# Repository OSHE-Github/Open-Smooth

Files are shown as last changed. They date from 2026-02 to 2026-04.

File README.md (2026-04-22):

# Open-Smooth

# Project Overview
OPENSmooth introduces an open-source 3D print post-processor that uses acetone vapor and heat to smooth filament layer lines. The system integrates electronic monitors to regulate exposure time and ensure safe operation, reducing risks associated with manual methods. By combining automated vapor control with real-time safety monitoring, the design provides a low-cost, accessible solution to improve the surface quality of 3D-printed parts.
# Bill of Materials

### Physical Construction
| Category | Item | Part Number | Source | Cost |
|---|---|---|---|---|
| Physical Construction | PETG filament | - | Amazon | $15 (per spool) |
| Physical Construction | Enclosure bin | - | Amazon | $12 |
| Physical Construction | Plastic bottles | - | Amazon | $7 |
| Physical Construction | Fan grill | - | Amazon | $5 |
| Physical Construction | Epoxy | - | Amazon | $8 |

### Electronics
| Category | Item | Part Number | Source | Cost |
|---|---|---|---|---|
| Electronics | Heater | - | Amazon | $35 |
| Electronics | Atomizers | - | Amazon | $23 |
| Electronics | Fans (x2) | - | Amazon | $18 |
| Electronics | E-stop | - | Amazon | $12 |
| Electronics | Touchscreen | - | Amazon | $16 |
| Electronics | Servo | - | Amazon | $19 |
| Electronics | IEC plug | - | Amazon | $8 |
| Electronics | IEC cable | - | Amazon | $6 |
| Electronics | RGB lights | - | Amazon | $13 |

### Circuitry
| Category | Item | Part Number | Source | Cost |
|---|---|---|---|---|
| Circuitry | PCB | - | - | $10 |
| Circuitry | Arduino Mega | - | - | $30 |
| Circuitry | ATMEGA328 (x2) | - | DigiKey | $6 |
| Circuitry | Relays (x2) | - | Amazon | $14 |
| Circuitry | Buck converters | - | Amazon | $8 |
| Circuitry | 2N2222A Transistors (x20) | - | DigiKey | $1 |
| Circuitry | Thermistor | - | - | $8 |
| Circuitry | Acetone sensor | - | - | $8 |
| Circuitry | 12V power supply | - | Amazon | $10 |

### Consumables
| Category | Item | Part Number | Source | Cost |
|---|---|---|---|---|
| Consumables | Acetone | - | Amazon | $10 |
| Consumables | Carbon pellets | - | Amazon | $12 |

---

## Tools Used

### Testing and Planning
| Category | Item | Part Number | Source | Cost |
|---|---|---|---|---|
| Testing and Planning | Breadboard | ZYJ-102 | Adafruit | $5.95 |
| Testing and Planning | Multimeter | Fluke 179 | Fluke | $479.99 |
| Testing and Planning | Oscilloscope | MSO6012A | Test Equity | $2955.00 |

### Assembly
| Category | Item | Part Number | Source | Cost |
|---|---|---|---|---|
| Assembly | Solder Iron | FX-888D | Hakko | $121.47 |
| Assembly | Dremel | - | Milwaukee | - |
| Assembly | Drill | - | Milwaukee | - |

### Programming
| Category | Item | Part Number | Source | Cost |
|---|---|---|---|---|
| Programming | Arduino IDE | Arduino IDE 2.3.2 | Arduino | $0 |

# Assembly Overview
### 1. Print All Components
- 3D print all required parts using PETG filament
- Base components (13 parts)
- Filter components (9 parts)
- Rotating table components (4 parts) + servo housing (1 part)
- Recommended to have ~2kg of filament available
- Use supports only where necessary (mainly the table)

### 2. Assemble the Base
- Fit all base components together using the dovetail joints
- Ensure correct orientation (parts only fit one way)
- Press-fit assembly should hold the structure together
- Apply epoxy if additional strength is needed

### 3. Prepare and Assemble the Lid
- Cut and drill openings for:
  - Heater (rear-center)
  - Filter (top-center)
- Mount heater:
  - Cut a circular hole for the heater body
  - Drill mounting holes
  - Install the gasket and secure the heater
- Mount filter:
  - Cut a square intake hole
  - Drill mounting holes (M3)
- Install a limit switch at the bottom edge of the lid to detect the open/closed state

### 4. Assemble and Install the Filter
- Assemble the main filter housing using M3 screws
- Install a 60 mm fan and secure it with M4 screws
- Prepare pellet drawer:
  - Epoxy if printed in two parts
  - Fill with carbon pellets
- Insert pellet drawer and secure with clips and screws
- Cut mounting holes and vent in enclosure
- Attach filter and gasket to enclosure

### 5. Install the Rotating Table System
- Mount the servo into the servo housing
- Route wires through housing cutouts
- Install housing into base (center cutout)
- Attach the spur gear to the servo shaft
- Install the table spacer and the rotating table
- Snap the fan grille into place

### 6. Assemble Atomizers
- Assemble each atomizer:
  - Insert wick into atomizer
  - Secure wick using trimmed nail or pin
- Extend wiring to reach the control PCB
- Repeat for all atomizers
- Fill with acetone and place into holders

### 7. Final Assembly & Integration
- Ensure all mechanical components are secured
- Verify moving parts (table rotation, fan clearance)
- Confirm proper placement of heater, filter, and sensors
- Connect electronics (fans, heater, atomizers, sensors, etc.)
- Perform a system check before operation

### 8. Final Checks
- Verify all fasteners are tight
- Ensure no air leaks around the filter and heater
- Confirm limit switch functionality
- Test electrical connections safely

**Note:**  
Epoxy is optional in most areas but recommended for long-term durability.

# Future Improvements
### Enclosure Stability and Sealing Capability
The enclosure currently uses duct tape to keep a seal with the lid. This works well, but it could be improved. Adding a lid locking mechanism with a layered rubber seal at the base would prevent the lid from unintentionally opening as well as provide a better seal.

### Atomizer bottles
The atomizer bottles we used for this project are made of PET plastic. PET plastic is susceptible to acetone over long periods of time, causing the bottles to likely leak. In our testing, the bottles showed minimal wear, but this doesn't mean they are 100% safe. Bottles made of PP or HDPE plastic would be much better suited for this application.

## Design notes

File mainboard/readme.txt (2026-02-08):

Here is the code and kicad progect for the mainboard and pcb

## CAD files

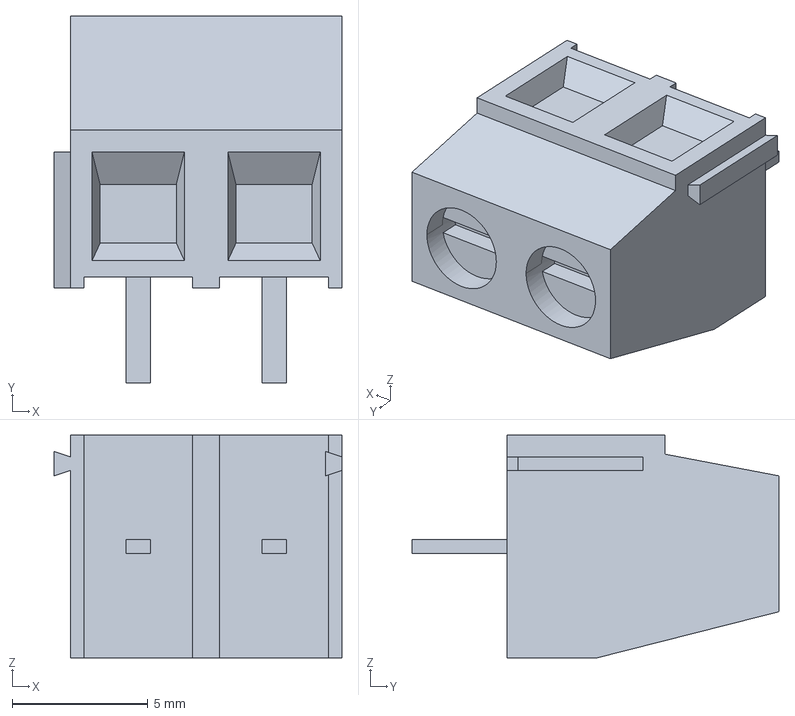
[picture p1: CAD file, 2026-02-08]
mainboard/pcb/KiCADv6/c-282836-2-j-3d.stp
10.6 x 13.5 x 8.20 mm

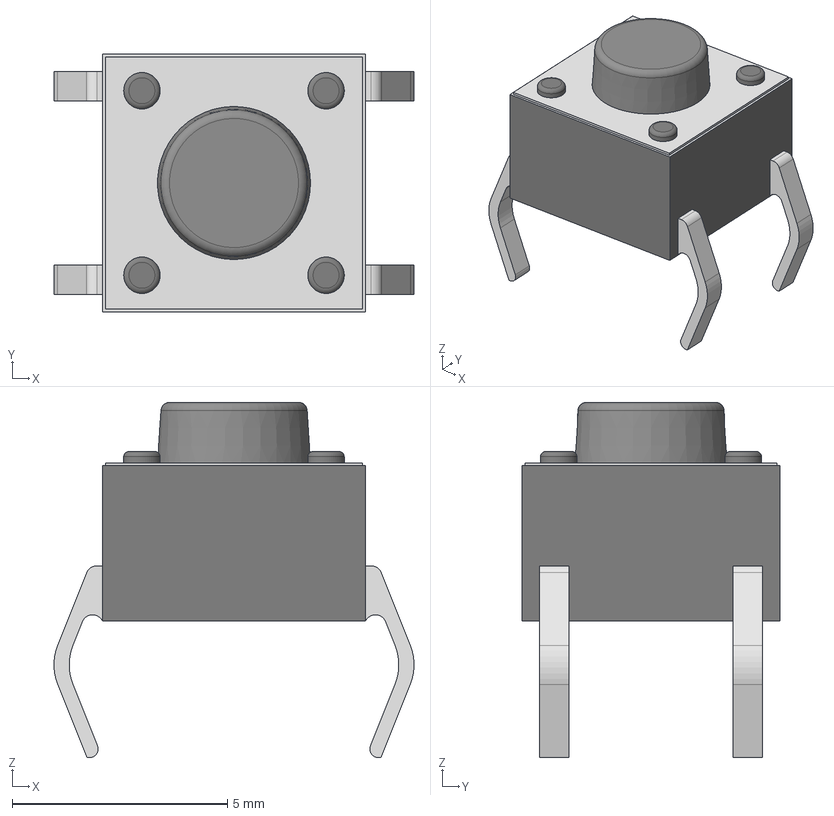
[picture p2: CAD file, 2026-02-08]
mainboard/pcb/Tactal Switch -THru (6mmx 6mmx5mm)-Black.stp
8.37 x 5.99 x 8.26 mm

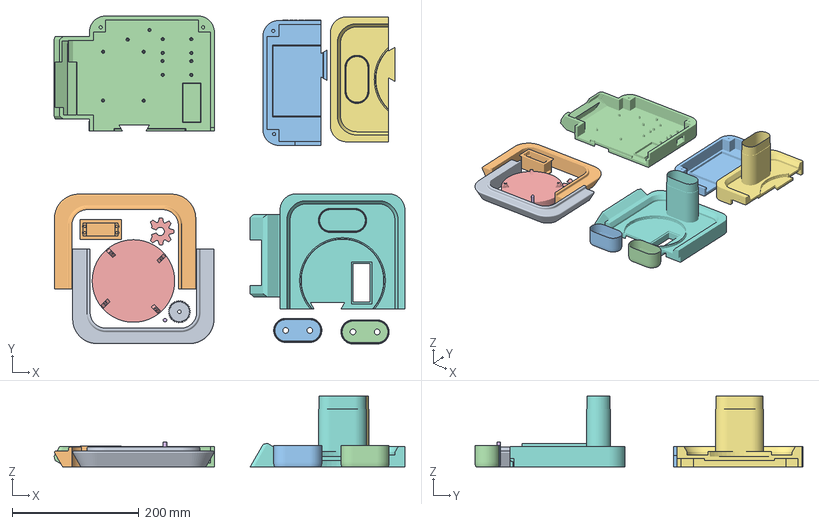
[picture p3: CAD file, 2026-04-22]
OPENSmooth_EnclosureS26 (1).3mf
552.9 x 516.8 x 111.6 mm
Final Assembly_48
Final Assembly_51
Final Assembly_53
Final Assembly_82
Final Assembly_93
Final Assembly_96
Final Assembly_67_A
Final Assembly_67_B
Final Assembly_92_A
Final Assembly_92_B
Final Assembly_16_A
Final Assembly_16_B
Revolving Table (1)

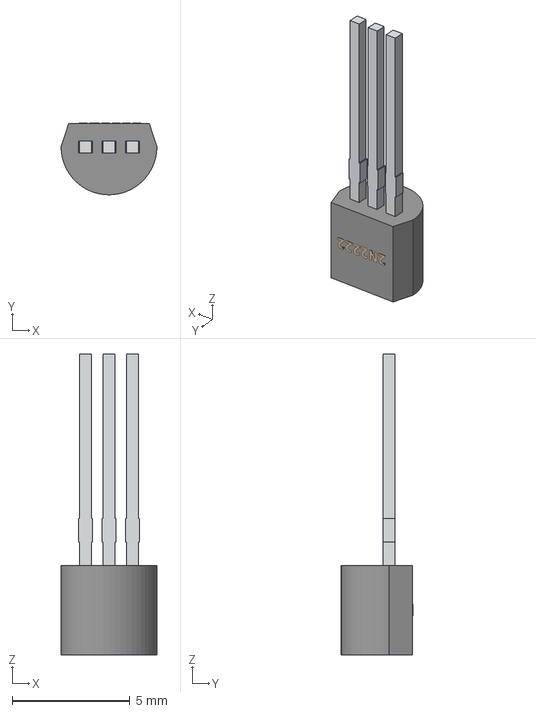
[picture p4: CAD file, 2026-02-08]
mainboard/pcb/2n2222.step
4.08 x 3.05 x 12.8 mm

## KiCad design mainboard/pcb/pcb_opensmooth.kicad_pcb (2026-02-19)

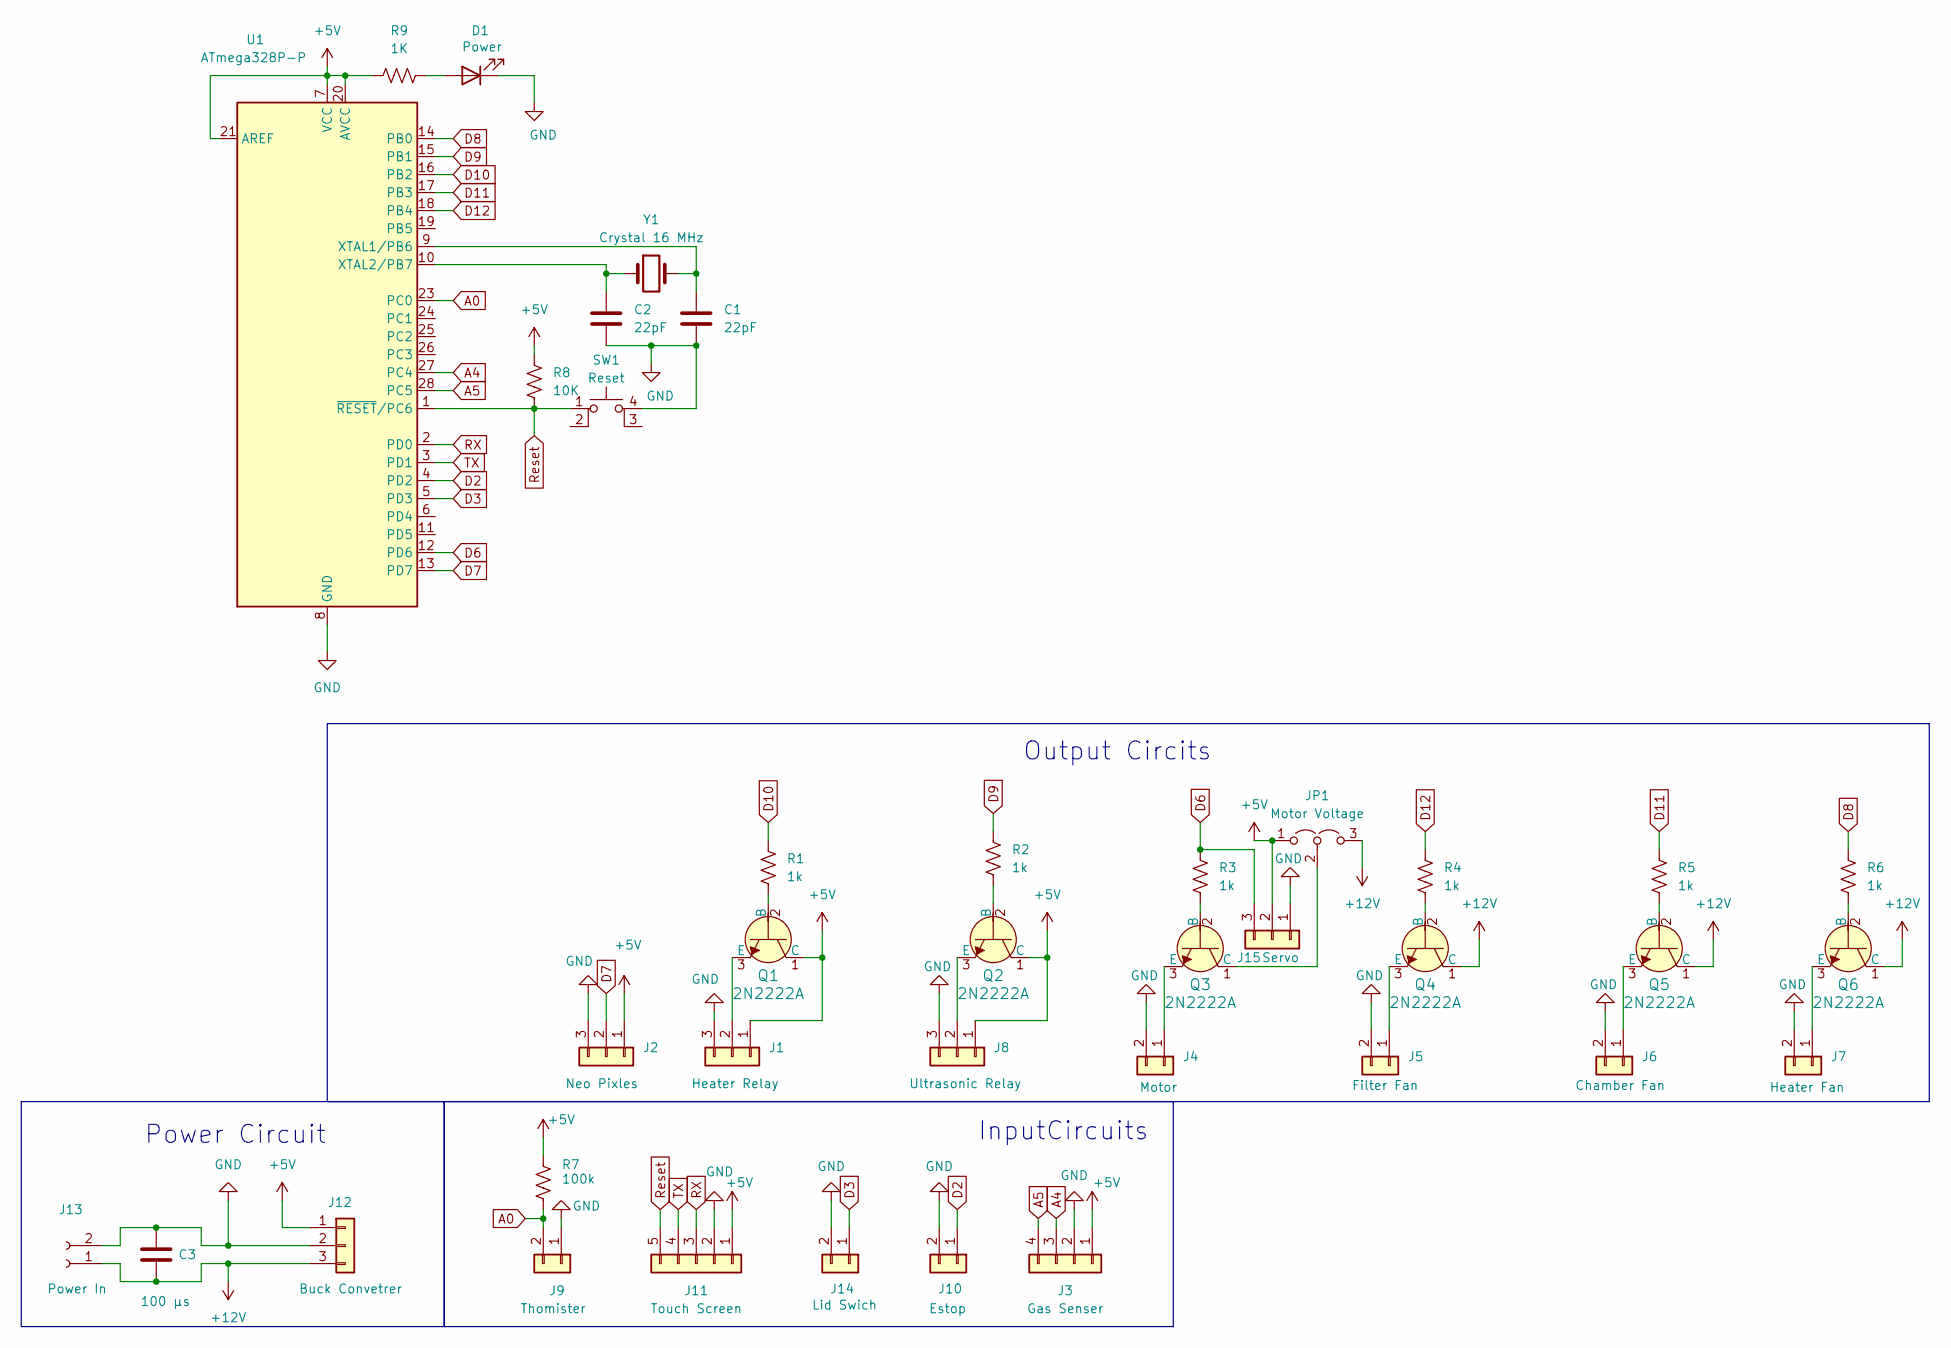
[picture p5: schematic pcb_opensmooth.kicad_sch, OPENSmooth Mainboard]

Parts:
C1, C2: 22pF; C_Disc_D3.0mm_W1.6mm_P2.50mm
C3: 100 μs; C_Radial_D6.3mm_H7.0mm_P2.50mm
D1: Power; LED_D5.0mm
J1: Heater Relay; JST_XH_B3B-XH-A_1x03_P2.50mm_Vertical
J2: Neo Pixles; JST_XH_B3B-XH-A_1x03_P2.50mm_Vertical
J3: Gas Senser; JST_XH_B4B-XH-A_1x04_P2.50mm_Vertical
J4: Motor; JST_XH_B2B-XH-A_1x02_P2.50mm_Vertical
J5: Filter Fan; JST_XH_B2B-XH-A_1x02_P2.50mm_Vertical
J6: Chamber Fan; JST_XH_B2B-XH-A_1x02_P2.50mm_Vertical
J7: Heater Fan; JST_XH_B2B-XH-A_1x02_P2.50mm_Vertical
J8: Ultrasonic Relay; JST_XH_B3B-XH-A_1x03_P2.50mm_Vertical
J9: Thomister; JST_XH_B2B-XH-A_1x02_P2.50mm_Vertical
J10: Estop; JST_XH_B2B-XH-A_1x02_P2.50mm_Vertical
J11: Touch Screen; JST_XH_B5B-XH-A_1x05_P2.50mm_Vertical
J12: Buck Convetrer; JST_XH_B3B-XH-A_1x03_P2.50mm_Vertical
J13: Power In; 282837-2_TYC
J14: Lid Swich; JST_XH_B2B-XH-A_1x02_P2.50mm_Vertical
J15: Servo; PinHeader_1x03_P2.54mm_Vertical
JP1: Motor Voltage; PinHeader_1x03_P2.54mm_Vertical
Q1, Q2, Q3, Q4, Q5, Q6: 2N2222A; 2n2222; MPN 2N2222A; Digi-Key_PN 2N2222ACS-ND
R1, R2, R3, R4, R5, R6: 1k; R_Axial_DIN0309_L9.0mm_D3.2mm_P12.70mm_Horizontal
R7: 100k; R_Axial_DIN0309_L9.0mm_D3.2mm_P12.70mm_Horizontal
R8: 10K; R_Axial_DIN0309_L9.0mm_D3.2mm_P12.70mm_Horizontal
R9: 1K; R_Axial_DIN0309_L9.0mm_D3.2mm_P12.70mm_Horizontal
SW1: Reset; Switch_Tactile_THT_6x6mm
U1: ATmega328P-P; DIP-28_W7.62mm
Y1: Crystal 16 MHz; Crystal_HC49-4H_Vertical

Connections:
+5V: J1.1, J2.1, J3.1, J8.1, J11.1, J12.1, J15.2, JP1.1 (A), Q1.1 (C), Q2.1 (C), R7.2, R8.2, R9.2, U1.7 (VCC), U1.20 (AVCC), U1.21 (AREF)
+12V: C3.2, J12.3, J13.1, JP1.3 (B), Q4.1 (C), Q5.1 (C), Q6.1 (C)
A0: J9.2, R7.1, U1.23 (PC0)
A4: J3.3, U1.27 (PC4)
A5: J3.4, U1.28 (PC5)
D2: J10.1, U1.4 (PD2)
D3: J14.1, U1.5 (PD3)
D6: J15.3, R3.2, U1.12 (PD6)
D7: J2.2, U1.13 (PD7)
D8: R6.2, U1.14 (PB0)
D9: R2.2, U1.15 (PB1)
D10: R1.2, U1.16 (PB2)
D11: R5.2, U1.17 (PB3)
D12: R4.2, U1.18 (PB4)
GND: C1.2, C2.2, C3.1, D1.1 (K), J1.3, J2.3, J3.2, J4.2, J5.2, J6.2, J7.2, J8.3, J9.1, J10.2, J11.2, J12.2, J13.2, J14.2, J15.1, SW1.4 (A), U1.8 (GND), U1.22 (GND)
unnamed: D1.2 (A), R9.1
unnamed: J1.2, Q1.3 (E)
unnamed: J4.1, Q3.3 (E)
unnamed: J5.1, Q4.3 (E)
unnamed: J6.1, Q5.3 (E)
unnamed: J7.1, Q6.3 (E)
unnamed: J8.2, Q2.3 (E)
unnamed: JP1.2 (C), Q3.1 (C)
unnamed: Q1.2 (B), R1.1
unnamed: Q2.2 (B), R2.1
unnamed: Q3.2 (B), R3.1
unnamed: Q4.2 (B), R4.1
unnamed: Q5.2 (B), R5.1
unnamed: Q6.2 (B), R6.1
unnamed: C1.1, U1.9 (XTAL1/PB6), Y1.2
unnamed: C2.1, U1.10 (XTAL2/PB7), Y1.1
RX: J11.3, U1.2 (PD0)
Reset: J11.5, R8.1, SW1.1, U1.1 (~RESET/PC6)
TX: J11.4, U1.3 (PD1)

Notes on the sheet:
InputCircuits
Output Circits
Power Circuit

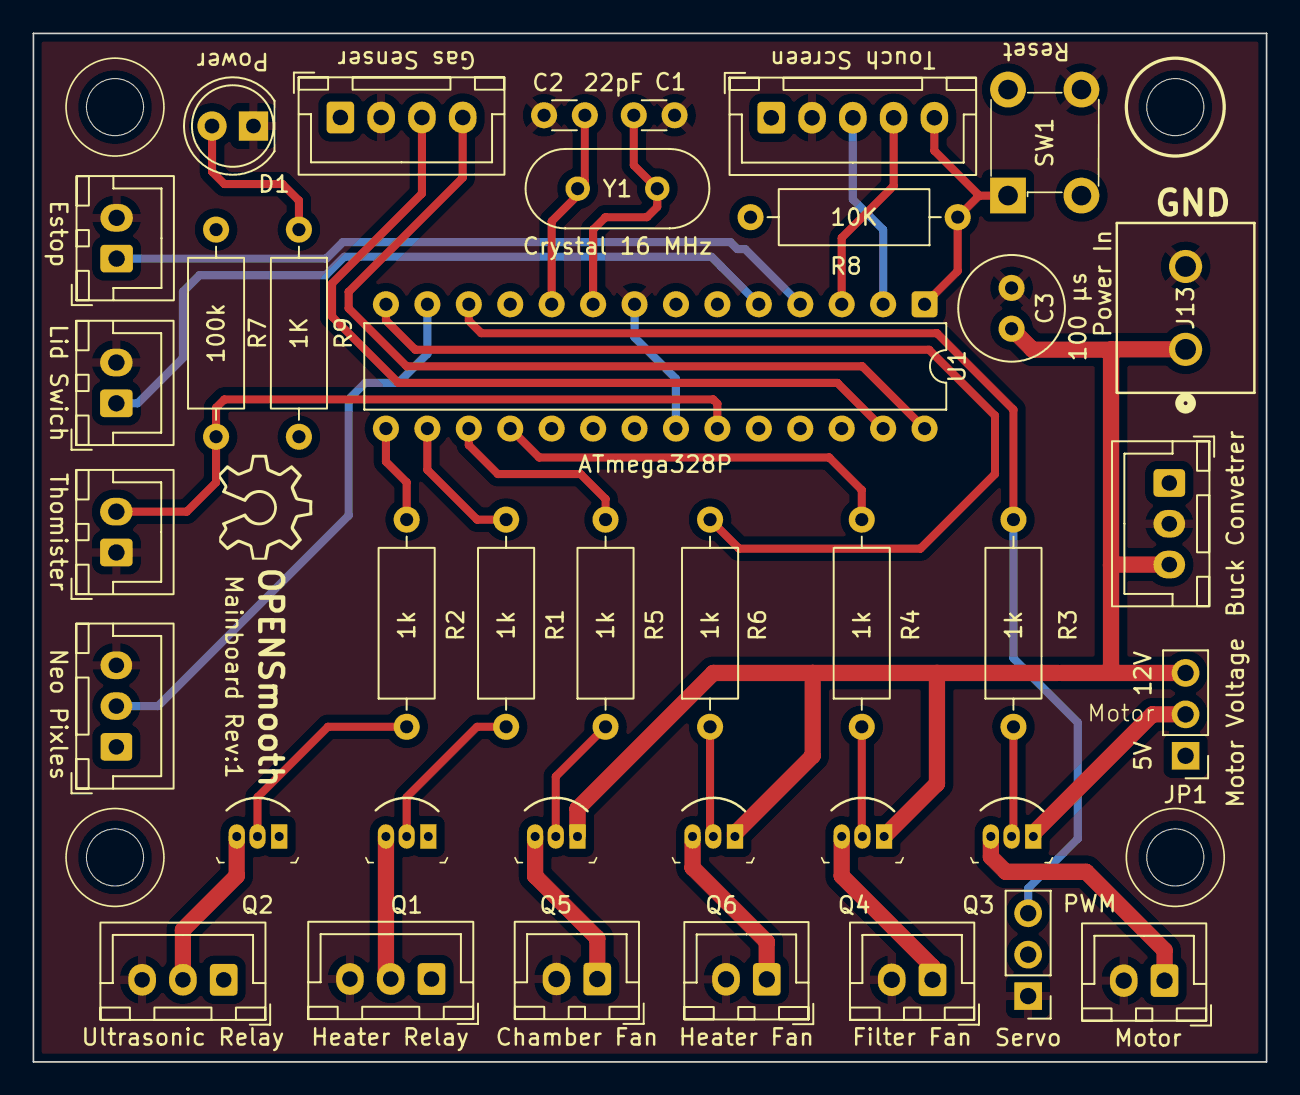
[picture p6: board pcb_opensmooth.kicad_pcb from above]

Board: 2 copper layers, 75.6 x 63.0 mm, 38 parts (0 on the bottom side), 34 nets.

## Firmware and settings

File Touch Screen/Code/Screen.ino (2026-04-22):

//incled parting file
#include "Parse.h"

//define touch screen and tft
TouchScreen ts = TouchScreen(XP, YP, XM, YM, 300);
Elegoo_TFTLCD tft(LCD_CS, LCD_CD, LCD_WR, LCD_RD, LCD_RESET);

int MButton = 67; 
int touchX = 180;
int touchY = 120;
int touchXOld = 180;
int touchYOld = 120;
uint16_t color[5][5];

//Setup code
void setup() {
  //start serial at 115200 baud rate
  Serial.begin(115200);
  Serial1.begin(115200);
  delay(1000);
  //mouse setup;
  pinMode(MButton, INPUT_PULLUP);
  pinMode(A11, INPUT);
  pinMode(A12, INPUT);



  //start tft and set roation
  tft.begin(0x9341);
  tft.setRotation(1);

  //pin setup for touchscreen and buzzer
  pinMode(13, OUTPUT);
  pinMode(SD_CS, OUTPUT);
  pinMode(buzzer+4, OUTPUT);
  digitalWrite(buzzer+4, LOW);
  pinMode(buzzer, OUTPUT);
  digitalWrite(LCD_CS, HIGH);
  pinMode(SD_CS, OUTPUT);
  digitalWrite(SD_CS, HIGH);

  delay(200);
  //inshalise SD card and report if failed
  if (!SD.begin(SD_CS)) {
    //Serial.println(F("SD failed!"));
    parse("Text(SD ERROR,50,100,4,65535)", tft);
    while (1)
      ;
  }


  //remove old files
  SD.remove(update);
  SD.remove(bFile);

  //run the starting file
  sd("begin.txt", tft);
  //mouse
  //mouse
  readColor();
}


//the runing body of the code
void loop() {

  //save screen touch to p
  digitalWrite(13, HIGH);
  TSPoint p = ts.getPoint();
  digitalWrite(13, LOW);
  pinMode(LCD_CS, OUTPUT);
  pinMode(LCD_CD, OUTPUT);

  mouse();
  //p.z = click();
  //check to see if screen was touched
  if (p.z > 15 || click()) {
    int temp = p.x;
    //convert the touch to quredents on screen
    p.x = map(p.y, 930, 40, 0, 320);
    p.y = map(temp, 900, 160, 0, 240);

    //mouse
    if(click()){
      p.x = touchX;
      p.y = touchY;
    }
    


    //extra delay to prevent double press
    delay(100);

    //check to see if a button was pressesd
    for (int i = 0; i < bCount; i++) {
      if (p.x > buttons[i][0] && p.x < buttons[i][2] && p.y > buttons[i][1] && p.y < buttons[i][3]) {

        //beep the buzzer
        for (int i = 0; i < 100000 / (2 * pitch) && Buzz; i++) {
          digitalWrite(buzzer, HIGH);
          delayMicroseconds(pitch);
          digitalWrite(buzzer, LOW);
          delayMicroseconds(pitch);
        }

        //if button was pressed open file and print line
        file = SD.open(bFile);
        //serch through the file until corect line is found
        for (int j = 0; j <= i; j++) {
          for (int k = 0; k < 40; k++) {
            Fileline[k] = file.read();
            if (Fileline[k] == 10) {
              Fileline[k] = 0;
              break;
            }
          }
        }
        //close the file
        file.close();
        delay(5);
        //run the file line
        parse(Fileline, tft);
        if (fileName[0] != 0) {
          sd(fileName, tft);
          fileName[0] = 0;
        }
        if (old == 1) {
          sd(OldFile, tft);
          old = 0;
        }
        parse("Run(text.txt)", tft);
        Time = millis();
        //mouse
        readColor();

        break;
      }
      
    }
  }

  if (Serial1.available()) {
    serial(Serial1.readStringUntil('\n').c_str(), tft);
    if (old == 1) {
      sd(OldFile, tft);
      old = 0;
    }
  }

  if (Time + UPDATE_TIME < millis()) {
    parse("Run(text.txt)", tft);
    x += 10;
    Time = millis();
  }
}

//mouse
int click(){
  if(!digitalRead(MButton)) return 30;
  return 0;
}
void mouse(){
  int Ax = analogRead(A11);
  int Ay = analogRead(A12);
  bool change = false;

  if(Ay < 300 && touchX < 315){
    touchX +=5;
    change = true;
  }
  if(Ay > 700 && touchX > 0){
    touchX -=5;
    change = true;
  }
  if(Ax > 700 && touchY < 235){
    touchY +=5;
    change = true;
  }
  if(Ax < 300 && touchY > 0){
    touchY -=5;
    change = true;
  }

  if(change){
    for(int i = 0; i < 5; i++){
      for(int j = 0; j < 5; j++){
        tft.drawPixel(touchXOld+i, touchYOld+j, color[i][j]);
        color[i][j] = tft.readPixel(touchX+i, touchY+j);
      }
    }
    touchXOld = touchX;
    touchYOld = touchY;
    tft.fillRect(touchX, touchY, 5, 5, 65535);
    tft.fillRect(touchX+1, touchY+1, 3, 3, 0);
    delay(15);
  }

}

void readColor(){
  for(int i = 0; i < 5; i++){
      for(int j = 0; j < 5; j++){
        color[i][j] = tft.readPixel(touchX+i, touchY+j);
      }
    }
    touchXOld = touchX;
    touchYOld = touchY;
    tft.fillRect(touchX, touchY, 5, 5, 65535);
    tft.fillRect(touchX+1, touchY+1, 3, 3, 0);
}

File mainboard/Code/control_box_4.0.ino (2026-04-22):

#include <Adafruit_NeoPixel.h>
#include <Servo.h>

#include "Thermister.h"
#include "Vars.h"
#include "Heater.h"
#include "Acetone.h"



//libray setup
NTC_100k tempSence(thmist);
RelayHeater heater(heaterPin, fan1, tempSence);
bomb acetone(ultrasonic, fanHeater);
Servo servo;
Adafruit_NeoPixel neo(ledCount, 7, NEO_GRB + NEO_KHZ800 );

void setup() {
  //inishalise Serial
  Serial.begin(115200);
  neo.begin();
  

  while (!Serial) { delay(10); }  // Wait for serial console to open
  //set up gas sencer in acetone
  acetone.Setup();
  //chamber fan setup
  pinMode(fanPin, OUTPUT);
  pinMode(button, INPUT_PULLUP);
  pinMode(encloser, INPUT_PULLUP);
  //estop
  //attachInterrupt(digitalPinToInterrupt(button), stop, LOW);
  //servo setup
  servo.attach(6);

  //screen turn on
  digitalWrite(fanPin,LOW);
  delay(1000);
  digitalWrite(fanPin,HIGH);
  //color(neo.Color(255, 255, 255));

}

void loop() {
  update(timer > 0);


  if (time + 2000 < millis()) {
    if (timer > 0) timer--;
    send();
    time = millis();
  }

  read();
}

//update sencers
//need to rewrite
void update(bool ace) {

  if (!digitalRead(button)){
    delay(500);
    if (!digitalRead(button)) stop();
  }

  if (digitalRead(encloser) == 1 && open) {
    //pauses system if lid is opened
    heater.run();
    acetone.run(ace);
    Serial.println("CLOSE");
    open = false;
  } else if (digitalRead(encloser) == 1) {
    //updates heater and acetone
    heater.run();
    acetone.run(ace);
  } else {
    //pauses system if lid is opened
    heater.pause();
    acetone.pause();
    servo.write(90);
    if(!open) Serial.println("OPEN");
    open = true;
  }
  //estop if max temp is reached
  //if (heater.read(false) >= heatMax) stop();
}

//reads in serial and sends to parce
void read() {
  String in;
  String comand;
  int space;
  double input;
  if (Serial.available()) {

    in = Serial.readStringUntil('\n');  // Read until newline
    space = in.indexOf(" ");            // find space
    if (space != -1) {
      //if there is a space split in comand in 2
      comand = in.substring(0, space);
      input = in.substring(space + 1).toDouble();
    } else {
      //only send comand
      comand = in;
      input = 0;
    }
    //send comands to be parsed
    set(comand, input);
  }
}

//parse the comand and give its input
void set(String comand, double input) {
  //all of the parsing
  comand.trim();
  if (comand.equalsIgnoreCase("setTemp")) heater.setTemp(input, farenhight);
  else if (comand.equalsIgnoreCase("setAcetone")) acetone.setAcetone(input);
  else if (comand.equalsIgnoreCase("setFilter")) {
    if (input == 0) acetone.runFilter(false);
    else acetone.runFilter(true);
  } else if (comand.equalsIgnoreCase("setHeatFan")) {
    if (input == 0) heater.runFan(false);
    else heater.runFan(true);
  } else if (comand.equalsIgnoreCase("setCircFan")) {
    if (input == 0) fan = false;
    else fan = true;
  } else if (comand.equalsIgnoreCase("setServo")) {
    if (input == 0) servo.write(90);
    else servo.write(105);
  } else if (comand.equalsIgnoreCase("Run")) {
    timer = (int)input;
  } else if (comand.equalsIgnoreCase("KILL")) {
    stop();
  } else if (comand.equalsIgnoreCase("RED")) {
    color(neo.Color(255, 0, 0));
  } else if (comand.equalsIgnoreCase("GREEN")) {
    color(neo.Color(0, 255, 0));
  } else if (comand.equalsIgnoreCase("BLUE")) {
    color(neo.Color(0, 0, 255));
  } else if (comand.equalsIgnoreCase("YELLOW")) {
    color(neo.Color(255, 255, 0));
  } else if (comand.equalsIgnoreCase("WHITE")) {
    color(neo.Color(255, 255, 255));
  } else if (comand.equalsIgnoreCase("PURPLE")) {
    color(neo.Color(135, 0, 255));
  } else if (comand.equalsIgnoreCase("BLACK")) {
    color(neo.Color(0, 0, 0));
  } else Serial.println("Unknown Comand");
}

//sets the leds a color
void color(uint32_t color) {
  for (int i = 0; i < ledCount; i++)
    neo.setPixelColor(i, color);
  neo.show();
}

//sends info to screen
void send() {
  Serial.print("TEMP ");
  Serial.println((int)heater.read(farenhight));
  Serial.print("TempTarget ");
  Serial.println((int)heater.curentSet(farenhight));
  Serial.print("ACETONE ");
  Serial.println((acetone.getAcetone()));
  Serial.print("AcetoneTarget ");
  Serial.println(((int)acetone.getPresent()));
  // Serial.print(" Fans: ");
  // if (heater.curentFan()) Serial.print(1);
  // else Serial.print(0);
  // if (acetone.getFilter()) Serial.print(1);
  // else Serial.print(0);
  // if (fan) Serial.print(1);
  // else Serial.print(0);
  // Serial.print(" Timer: ");
  // Serial.println(timer);
}

//estop. stop all prosesed exsept fan
void stop() {
  detachInterrupt(digitalPinToInterrupt(button));
  heater.kill();
  acetone.kill();
  servo.write(90);
  digitalWrite(fanPin, HIGH);
  // Serial.println("KILL");
  while (true)
    Serial.println("KILL");
}

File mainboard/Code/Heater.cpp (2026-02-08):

// Author: Austin Deegan
// Date: 10/20/25
// Discription: controls a heater with bang bang controls

#include "Heater.h"
#include "Thermister.h"
#include <Arduino.h>

//vars
static double target = 0;
static int pin2, fan0;
static NTC_100k heat(0);
static bool fanP = false;
static unsigned long time = 0;
static int milliSec = 3000;
static bool fire = false;
//inishalise. Input <heater pin> <fan pin> <NTC_100k object>
RelayHeater::RelayHeater(int pin, int fan, NTC_100k thermister){ 
  pinMode(pin, OUTPUT);
  pinMode(fan, OUTPUT);
  pin2 = pin;
  fan0 = fan;
  heat = thermister;
}

// Sets the target tempacher. 0 to disable. 
//Must constently call run or will over heat.
//Input <temp in F or C> <True if Farenhight> 
double RelayHeater::setTemp(double Temp, bool Faren){
  double old = Temp;
  target = Temp;
  if(Faren) target = (target - 32) * 5/9;
  return old;
}

// Shuts off the heater. No longer need to call run 
void RelayHeater::kill(){
  target = 0;
  digitalWrite(pin2,LOW);
  digitalWrite(fan0,HIGH);
}

//disables heater until next run comand
void RelayHeater::pause(){
  digitalWrite(pin2,LOW);
}

//Returns the tempacher of the heater.
//Input <True if want in Farenhight> 
double RelayHeater::read(bool Faren){
  return heat.read(Faren);
}

//Returns if fan is on (true) or off (false)
bool RelayHeater::curentFan(){
  return fanP;
}

//Manulay control a fan
//Input <set true to run fan> 
void RelayHeater::runFan(bool on){
  if(on) digitalWrite(fan0,HIGH);
  else digitalWrite(fan0,LOW);
  fanP = on;
}

//Returns the curent target of the heater
//Input <True if want in Farenhight> 
double RelayHeater::curentSet(bool Faren){
  if(Faren && target!=0) return ((target * 9.0/5)+32); // converted to farenhight
  return target;
}

// MUST constntly call to run the heater
//curently bad and untested implemented
void RelayHeater::run(){
  if(target > 10){
     digitalWrite(fan0,HIGH);
     fanP = true;
  }
  // else{
  //   digitalWrite(fan0,LOW);
  //    fanP = false;
  // }
  if(heat.read(false)/10<target && target>0 && time + milliSec < millis() ){
    digitalWrite(pin2,HIGH);
    fire = true;
  }
  else{
    digitalWrite(pin2,LOW);
    if(fire){
      fire = false;
      time = millis();
    }
  } 
}
